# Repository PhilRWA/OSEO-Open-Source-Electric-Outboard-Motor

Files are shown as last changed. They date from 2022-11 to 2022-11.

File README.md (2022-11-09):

# Open-Source-Electric-Outboard-Motor
A simple 3d printed electric outboard motor for small boats.

This project is aiming to create a simple easy to assemble relatively high power and budget friendly electric outboard primarily for cruising yacht tenders and small dinghys. It is currently based around a VESC speed controller and a 6374 electric skateboard motor. 

The aims are to use cheap easy to obtain parts to create something that can compete with the torqueedo travel series of electric motors and certainly outperform cheaper trolling motors. Most parts are 3d printed with the exception of the transom mount and main shaft/ control arm which are made of 28mm and 22mm pole respectively. This means that unless you already have a 3d printer or know someone who does this project will become considerably more expensive. I'm printing all of the parts on my stock Ender 3 v2 in PETG without any issues.

I'm not planning to add much complexity to the electronics side of things if I can avoid it to keep things as accessible as possible for all people interested in building one of these. Although who knows, I'm sure it would be possible to add things like displays, gps speedometers, nav lights, and many other parts if you wanted to modify the design somewhat.

Currently I'm powering the system with a 36v ebike battery, which is cheap and easy to obtain, but this does have a drawback of only being able to supply around 1/3 of the wattage that the motor can handle. This is still around 900w which is 50% more power than the torqueedo travel I believe, so I'm hoping it will still perform well, and you can unlock more performance by either building or buying a battery capable of supplying a higher continuous current. I wil be designing a dedicated battery pack for this at some stage, but first I need to build one and confirm my theories work.

Currently the estimated cost for the project (assuming you already have a 3d printer) is around £400 including the 36v e bike battery, which is a pretty attractive option given a torqueedo is around £1500 last time I checked.

So I'll be hopefully updating here as things progress, and I will update on performance as soon as I can get around to building the version 1. If anyone wants to send me any suggestions or ideas for improvements or things that I have overlooked feel free to mention it on here.

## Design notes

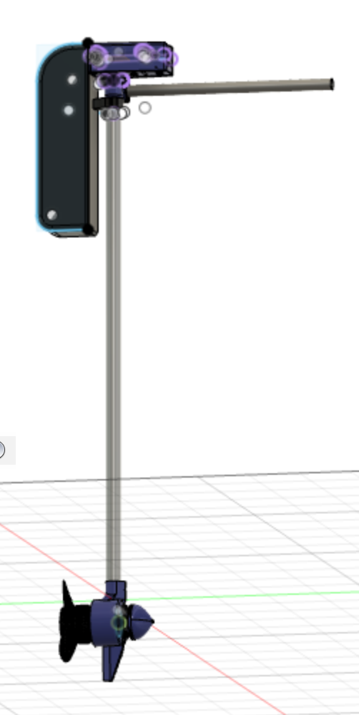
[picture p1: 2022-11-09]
OSEO screen grab.png

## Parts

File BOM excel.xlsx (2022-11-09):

OSEOM Bill of Materials V1
Category | Description | Qty | Notes | Optional? | Price | Purchase link
Printed Parts | Control box base | 1 | Approximate price for 2kg of PETG filament, which should be more than enough |  | £40.00
 | Control box top | 1 |  |  |  | Total cost:
 | Bar top/arm mount | 1 |  |  |  | £386.77
 | Prop housing | 1
 | Prop housing cover | 1
 | Prop | 1
 | Battery grip part 1 | 1
 | Battery grip part 2 | 1
 | Bar grip part 1 | 1
 | Bar grip part 2 | 1
 | Skeg | 1 | If printing this use prop housing with keg to create the cut out | Y
Electronics | Flipsky VESC 75100 | 1 |  |  | £91.02 | https://www.aliexpress.com/item/1005003980571005.html?spm=a2g0o.order_list.0.0.55b81802cw8Hb8
 | 6374 Motor 2800w | 1 | Can modify to any 63 diameter motor easily enough I imagine |  | £44.27 | https://www.aliexpress.com/item/4001261092425.html?spm=a2g0o.order_list.0.0.55b81802cw8Hb8
 | E bike throttle | 1 | Avoid any with key switches ideally |  | £14.21 | https://www.aliexpress.com/item/1005003972821513.html?spm=a2g0o.order_list.0.0.55b81802cw8Hb8
 | 19mm halo switch | 2 | price includes pigtails |  | £6.10 | https://www.aliexpress.com/item/4001291695467.html?spm=a2g0o.order_list.0.0.55b81802cw8Hb8
 | Pigtails for halo switch | 2 | Can just solder wires to switch to save a few quid if preferred | Y |  | https://www.aliexpress.com/item/4001023686738.html?spm=a2g0o.order_list.0.0.55b81802cw8Hb8
 | HM-10 BLE module | 1 |  | Y | £4.85 | https://www.aliexpress.com/item/32516357718.html?spm=a2g0o.order_list.0.0.55b81802cw8Hb8
 | 7 Pin JST 2.0 | 1 | get extra as spare in case of mistakes | Y
 | 6 Pin JST 2.0 Sockets and assembly | 2 | get extra as spare in case of mistakes | Y
 | 25 x 64mm PCB strip board | 1 |  | Y
 | 4.0 motor connector pairs | 6 | Price for 5 pairs, I’m one short |  | £3.08 | https://www.aliexpress.com/item/4000439855711.html?spm=a2g0o.order_list.0.0.55b81802cw8Hb8
 | Outboard kill switch | 1 |  |  | £7.01 | https://www.aliexpress.com/item/1005002241288096.html?spm=a2g0o.order_list.0.0.55b81802cw8Hb8
 | XT90 Anti Spark F | 2 | Price for 5 pairs |  | £14.99 | https://www.amazon.co.uk/gp/product/B087BYXJ8S/ref=ppx_yo_dt_b_asin_title_o06_s02?ie=UTF8&psc=1
 | XT90 Anti Spark M | 2 |  |  |  | same as above
 | GX16 plug and socket | 1 | Can modify for any 3 pin plug/socket of choice, price is for 8 pairs I think |  | £7.34 | https://www.aliexpress.com/item/4000825815868.html?spm=a2g0o.order_list.0.0.55b81802cw8Hb8
Fasteners | M3 heat set insert |  | One link for kit to cover all inserts |  | £6.49 | https://www.amazon.co.uk/gp/product/B08CR2XBLZ/ref=ppx_yo_dt_b_asin_title_o05_s00?ie=UTF8&psc=1
 | M4 heat set insert
 | M5 heat set insert
 | M3 flat head bolt 10mm |  | One purchase link for all bolts in project |  | £11.99 | https://www.amazon.co.uk/gp/product/B0924RF77X/ref=ppx_yo_dt_b_asin_title_o01_s01?ie=UTF8&psc=1
 | M3 flat head bolt 20mm
 | M3 flat head bolt 30mm
 | M4 flat head bolt 10mm
 | M4 flat head bolt 20mm
 | M4 flat head bolt 30mm
 | M5 flat head bolt 10mm
 | M5 flat head bolt 20mm
 | M5 flat head bolt 30mm
 | M3 washer |  | Price for set to cover all in project |  | £9.99 | https://www.amazon.co.uk/HSEAMALL-Washers-assorted-Insulating-500-Pack/dp/B07CJ98WG2
 | M3 rubber washer
 | M4 washer
 | M4 rubber washer | 28?
 | M5 washer
 | M5 rubber washer
 | M5 Spring washer | 1
Other parts | Transom assembly | 1 | Could 3d print something if preferred |  | £31.84 | https://www.aliexpress.com/item/1005003391879296.html?spm=a2g0o.order_list.0.0.55b81802cw8Hb8
 | E bike 36v battery | 1 | Can use any 36v battery that can supply 25a continuous or more. Optional custom pack to come later |  | £72.38 | https://www.aliexpress.com/item/1005004783301433.html?spm=a2g0o.order_list.0.0.55b81802cw8Hb8
 | Oil seal 60mm x 85mm x 10mm | 1 |  |  | £8.44 | https://simplybearings.co.uk/shop/p25201/68x85x10mm-Nitrile-Rubber-Rotary-Shaft-Oil-Seal-with-Garter-Spring-R21-/-SC/product_info.html
 | Velcro strap | ~ | Optional extra securing for bike battery | Y
 | 28mm Aluminium pipe 1m | 1 | Can also use copper? Other materials? Can also be longer shorter as per your boats needs |  | £7.87 | https://www.aluminium-online.co.uk/product/28mm-x-2mm-aluminium-round-tube/
 | 22.2mm aluminium pipe 500mm | 1 | Can also use copper? Other materials? |  | £4.90 | https://www.aluminium-online.co.uk/product/7-8-x-16swg-aluminium-round-tube/
Consumables | 2 part epoxy for part bonding | 1
 | Silicone grease (or vaseline?) for oil seal packing | 1

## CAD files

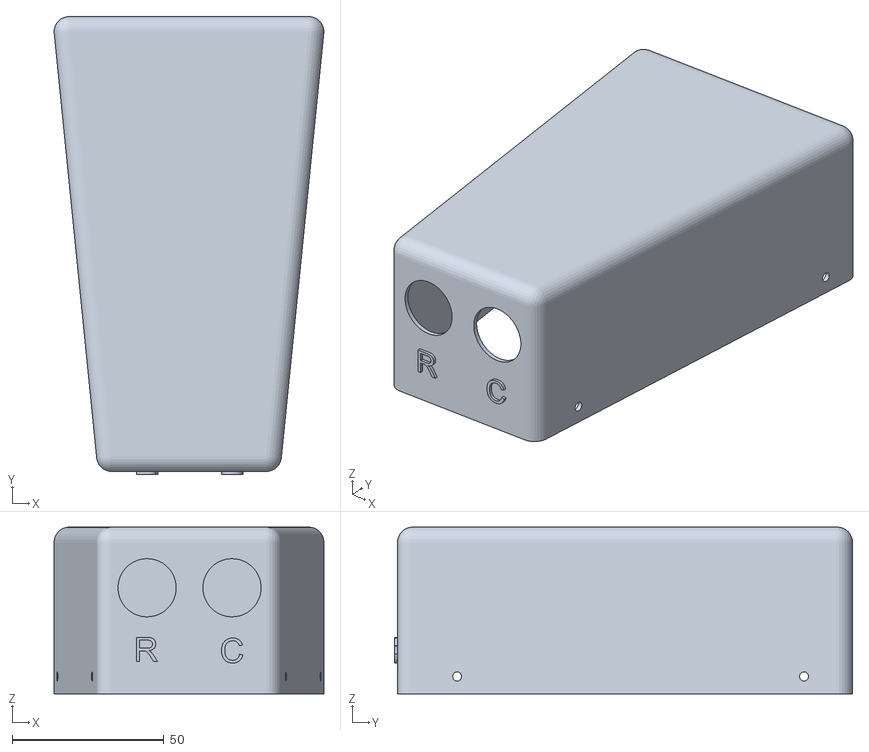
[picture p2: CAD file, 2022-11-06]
STLs/V1/Control box top v1.stl
88.9 x 151.0 x 55.0

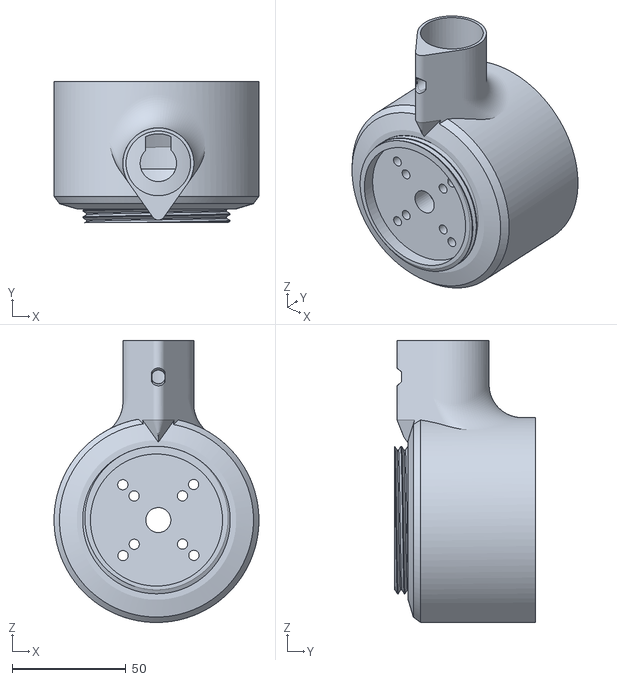
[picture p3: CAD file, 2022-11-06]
STLs/V1/Prop housing v1.stl
90.0 x 62.0 x 123.8

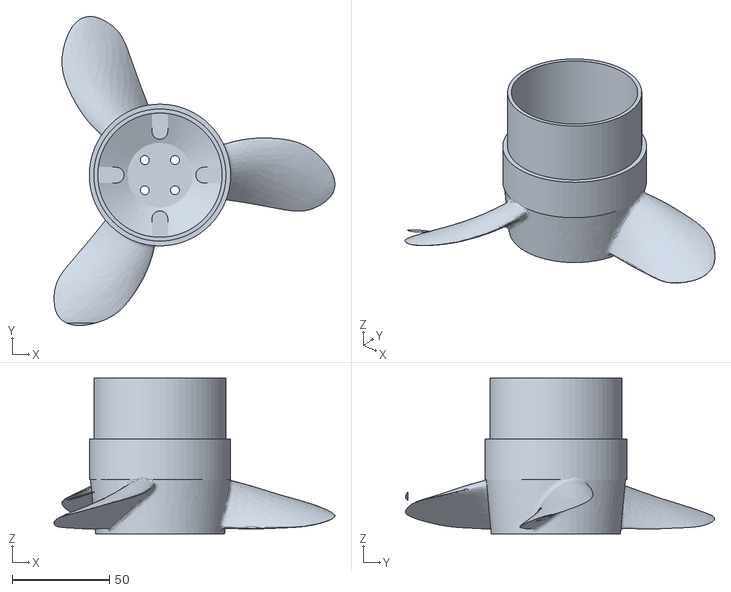
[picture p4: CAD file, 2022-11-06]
STLs/V1/Prop v1 (tinkercad).stl
144.6 x 159.0 x 80.3

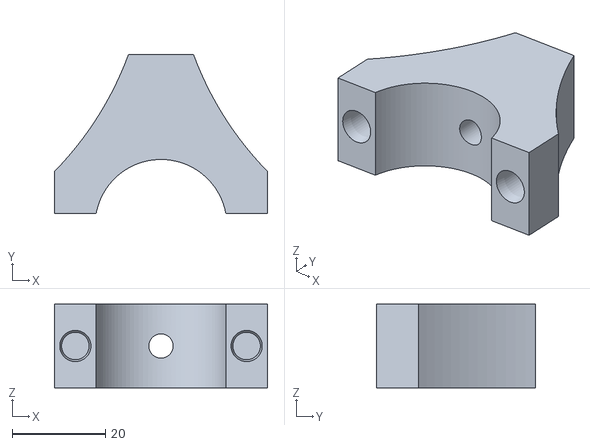
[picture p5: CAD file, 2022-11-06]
STLs/V1/Battery grip part 1 v1.stl
45.7 x 34.1 x 18.0

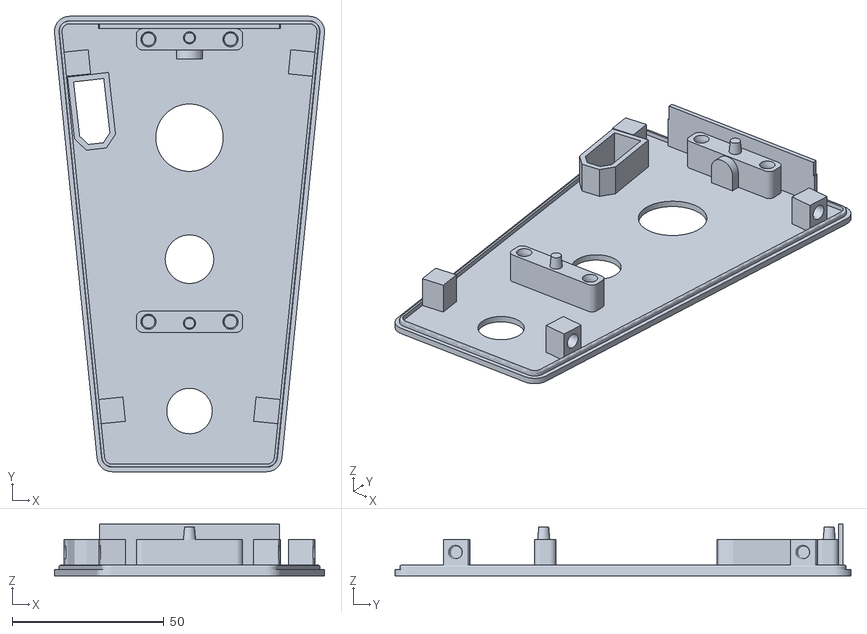
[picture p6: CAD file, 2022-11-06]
STLs/V1/Electronics floor v1.stl
88.9 x 150.0 x 17.0

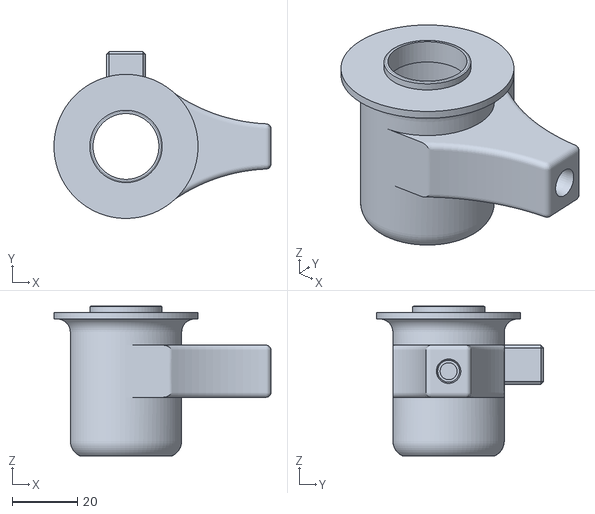
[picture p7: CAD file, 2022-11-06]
STLs/V1/Bar top:arm mount v1.stl
66.6 x 51.2 x 46.0

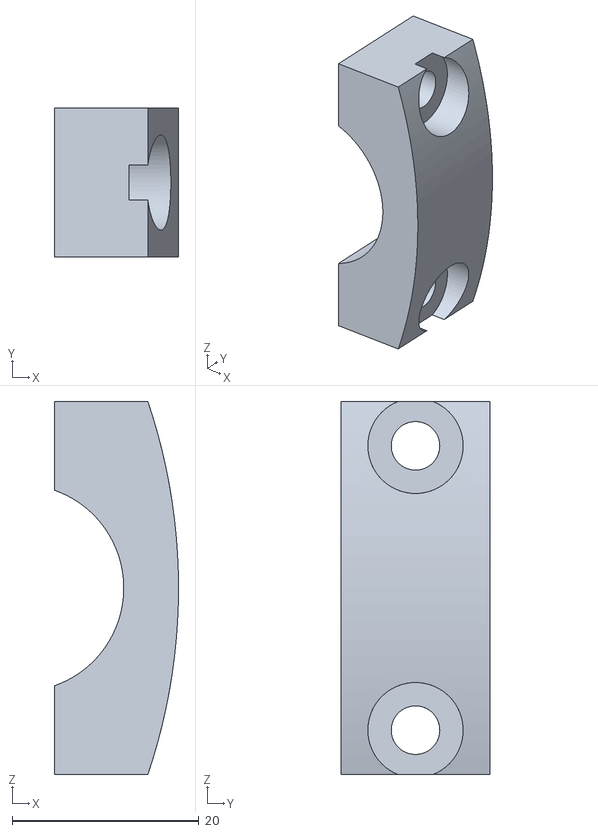
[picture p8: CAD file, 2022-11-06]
STLs/V1/bar grip part 2 v1.stl
13.3 x 16.0 x 39.9

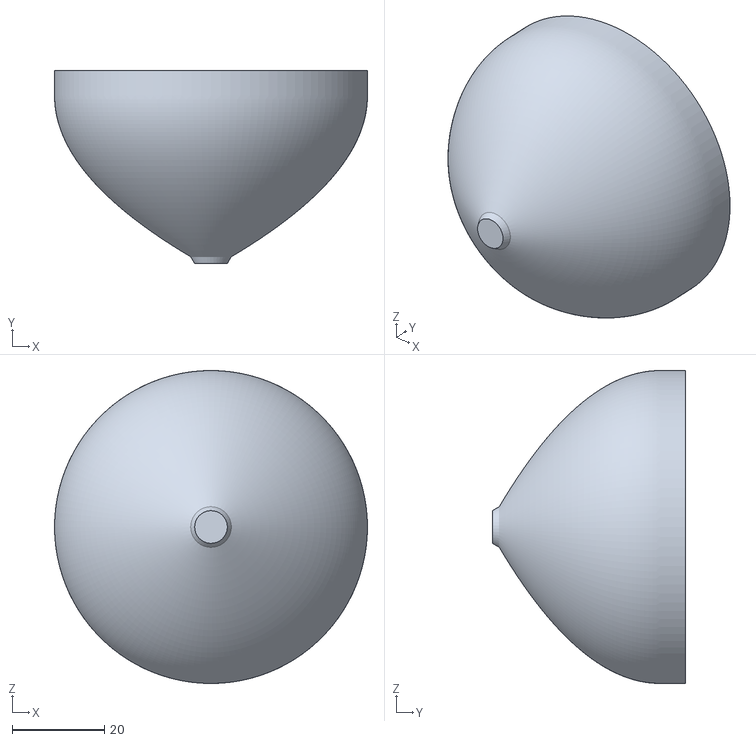
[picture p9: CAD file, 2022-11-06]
STLs/V1/Prop housing cover v1.stl
68.0 x 42.0 x 68.0

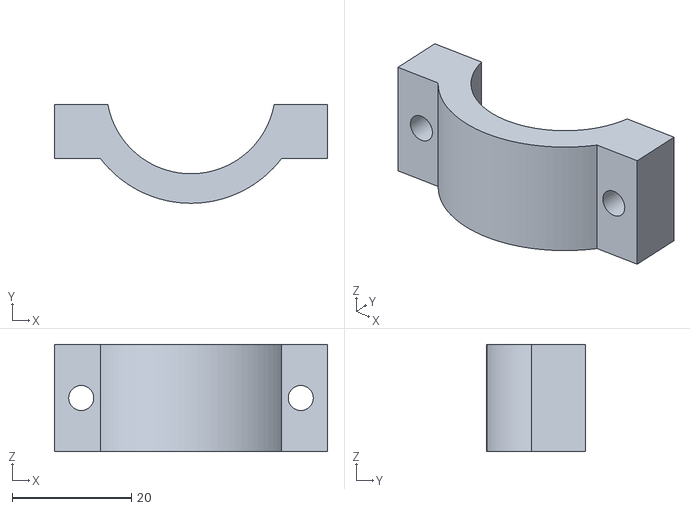
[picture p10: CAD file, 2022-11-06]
STLs/V1/Battery grip parrt 2 v1.stl
45.7 x 16.5 x 18.0

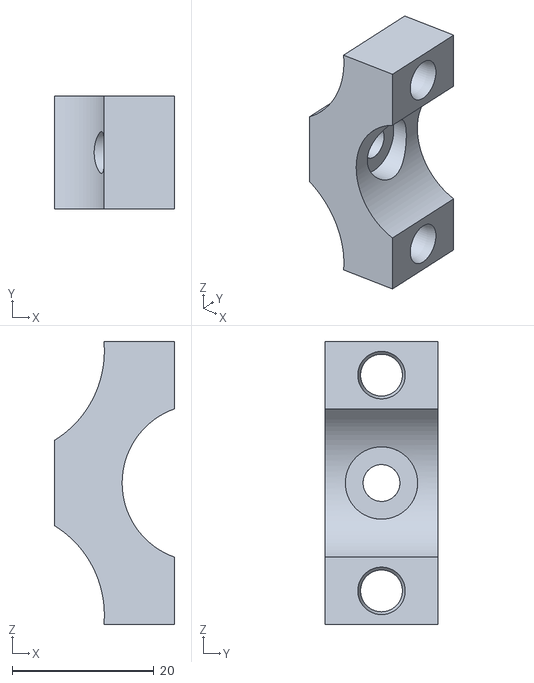
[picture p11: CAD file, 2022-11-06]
STLs/V1/Bar grip part 1 v1.stl
17.0 x 16.0 x 39.9

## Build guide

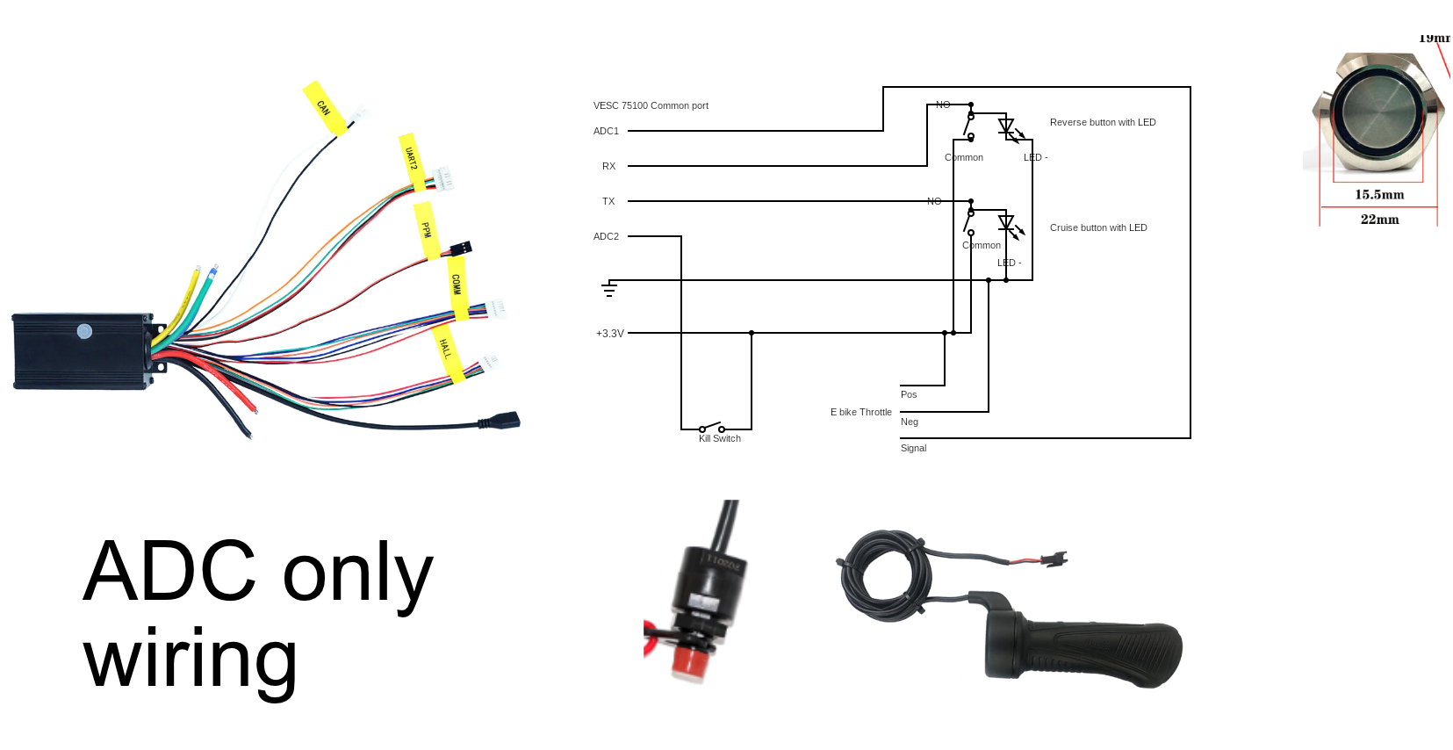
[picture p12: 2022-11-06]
ADC wiring diagram v1.jpg
